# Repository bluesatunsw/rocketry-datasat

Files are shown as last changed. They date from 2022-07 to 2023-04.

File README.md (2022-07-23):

# rocketry-datasat
Cubesat-shaped data collection payload for Rocketry's Griffon rocket. Intended as a simple payload for the launch with the added benefit of being a helpful exercise for our satellite team. Deployment and recovery are not our problem.

## Specifications
- L3 M1590 motor.
- 1U cubesat formfactor (100mm\*100mm\*100mm).
- Practically unlimited weight limit.
- < 45 minutes waiting time on pad; system batteries must last this long at least.
- Max idle temperature on pad: 50 degrees.
- 4.74 seconds acceleration, at least that long decceleration, but probably longer. Up to 50G.
- Apogee (altitude ceiling): 3050 metres.

## Git Hygiene guide

For this project we will be using standard software engineering principles for our version control.

### Branches and forks

The most important of these is to **make sure to make a fresh pull request for every new feature**. If you want to work on the main repo, this also means a new branch for every feature. If you are using forks, you can branch as you please.

In this case a "feature" is any atomic piece of work you might be contributing, i.e. small enough that you are the only one likely to be working on it. For example, if you are working in /hardware you might implement the module to translate celestial coordinates to motor positions as a feature.

In the case that you are working on a bigger part with another person (or people) you can make a branch with sub-branches for each feature.

### Code review and pull requests

**Never commit directly to main**. The only exception to this is for making administrative changes like editing the readme, .gitignore, .codeowners and so on.
Whenever you finish a feature on a branch like described above, you should submit a **pull request** to get it merged back into a parent branch. Pull requests are also known as "merge requests" on GitLab and some other services (far clearer name frankly) because they basically give you a chance to write up what you've done and documents all the changes you are going to make. It also lets you safely specify how you are going to handle any conflicts between your branch and the parent.

Once you have made your pull request you should ideally get somebody else who didn't contribute to do a **code review** for you. This is mostly important on larger features or things where a lot can go wrong. While this project doesn't have critical stakes or a deployment to risk, it's a very important habit and will often catch a lot of mistakes that are very hard to find on your own (especially when they are errors in design rather than in code).

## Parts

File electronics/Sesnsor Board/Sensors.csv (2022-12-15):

Source: | D:\Sensor Board\Sensors\Sensors.kicad_sch
Date: | 14/10/2022 6:08:25 PM
Tool: | Eeschema (6.0.6)
Generator: | C:\Program Files\KiCad\6.0\bin\scripting\plugins/bom_csv_grouped_by_value.py
Component Count: | 15
Individual Components:
Item | Qty | Reference(s) | Value | LibPart | Footprint | Datasheet | MANUFACTURER | MAXIMUM_PACKAGE_HEIGHT | PARTREV | STANDARD
 |  | Board1 | Rocket_Board | BlueSat:Rocket_Board | IMU:Rocket_Layout
 |  | C1 | 1 uF | Device:C | Capacitor_SMD:C_0201_0603Metric_Pad0.64x0.40mm_HandSolder | ~
 |  | J1 | GY-91 | Connector:Conn_01x08_Female | Connector_PinHeader_2.54mm:PinHeader_1x08_P2.54mm_Vertical | ~
 |  | J2 | JTAG | Connector_Generic:Conn_01x04 | Connector_PinHeader_2.54mm:PinHeader_1x04_P2.54mm_Vertical | ~
 |  | J3 | UART | Connector_Generic:Conn_01x04 | Connector_PinHeader_2.54mm:PinHeader_1x04_P2.54mm_Vertical | ~
 |  | MicroSD1 | Conn_01x06 | Connector_Generic:Conn_01x06 | Connector_PinHeader_2.54mm:PinHeader_1x06_P2.54mm_Vertical | ~
 |  | PC1 | C | Device:C | Capacitor_SMD:C_0201_0603Metric_Pad0.64x0.40mm_HandSolder | ~
 |  | R1 | 10K | Device:R | Resistor_SMD:R_0201_0603Metric_Pad0.64x0.40mm_HandSolder | ~
 |  | R_{SCL}1 | 4,7K | Device:R_Small | Resistor_SMD:R_0603_1608Metric_Pad0.98x0.95mm_HandSolder | ~
 |  | R_{SDA}1 | 4,7K | Device:R_Small | Resistor_SMD:R_0603_1608Metric_Pad0.98x0.95mm_HandSolder | ~
 |  | Si7021 | Conn_01x05 | Connector_Generic:Conn_01x05 | Connector_PinHeader_2.54mm:PinHeader_1x05_P2.54mm_Vertical | ~
 |  | SW1 | SW_Push | Switch:SW_Push | Button_Switch_SMD:SW_SPST_B3U-1000P | ~
 |  | SW2 | SW_Push | Switch:SW_Push | Button_Switch_SMD:SW_SPST_B3U-1000P | ~
 |  | U1 | ESP32-WROOM-E | ESP32:ESP32-WROOM-E | Espressif:ESP32-WROOM-32E | https://www.espressif.com/sites/default/files/documentation/esp32-wroom-32e_esp32-wroom-32ue_datasheet_en.pdf
 |  | U2 | H3LIS100DLTR | IMU:H3LIS100DLTR | PQFN50P300X300X100-16N |  | STMicroelectronics | 1 mm | 2 | IPC 7351B
Collated Components:
Item | Qty | Reference(s) | Value | LibPart | Footprint | Datasheet | MANUFACTURER | MAXIMUM_PACKAGE_HEIGHT | PARTREV | STANDARD
1 | 1 | Board1 | Rocket_Board | BlueSat:Rocket_Board | IMU:Rocket_Layout
2 | 1 | C1 | 1 uF | Device:C | Capacitor_SMD:C_0201_0603Metric_Pad0.64x0.40mm_HandSolder | ~
3 | 1 | J1 | GY-91 | Connector:Conn_01x08_Female | Connector_PinHeader_2.54mm:PinHeader_1x08_P2.54mm_Vertical | ~
4 | 1 | J2 | JTAG | Connector_Generic:Conn_01x04 | Connector_PinHeader_2.54mm:PinHeader_1x04_P2.54mm_Vertical | ~
5 | 1 | J3 | UART | Connector_Generic:Conn_01x04 | Connector_PinHeader_2.54mm:PinHeader_1x04_P2.54mm_Vertical | ~
6 | 1 | MicroSD1 | Conn_01x06 | Connector_Generic:Conn_01x06 | Connector_PinHeader_2.54mm:PinHeader_1x06_P2.54mm_Vertical | ~
7 | 1 | PC1 | C | Device:C | Capacitor_SMD:C_0201_0603Metric_Pad0.64x0.40mm_HandSolder | ~
8 | 1 | R1 | 10K | Device:R | Resistor_SMD:R_0201_0603Metric_Pad0.64x0.40mm_HandSolder | ~
9 | 2 | R_{SCL}1, R_{SDA}1 | 4,7K | Device:R_Small | Resistor_SMD:R_0603_1608Metric_Pad0.98x0.95mm_HandSolder | ~
10 | 1 | Si7021 | Conn_01x05 | Connector_Generic:Conn_01x05 | Connector_PinHeader_2.54mm:PinHeader_1x05_P2.54mm_Vertical | ~
11 | 2 | SW1, SW2 | SW_Push | Switch:SW_Push | Button_Switch_SMD:SW_SPST_B3U-1000P | ~
12 | 1 | U1 | ESP32-WROOM-E | ESP32:ESP32-WROOM-E | Espressif:ESP32-WROOM-32E | https://www.espressif.com/sites/default/files/documentation/esp32-wroom-32e_esp32-wroom-32ue_datasheet_en.pdf
13 | 1 | U2 | H3LIS100DLTR | IMU:H3LIS100DLTR | PQFN50P300X300X100-16N |  | STMicroelectronics | 1 mm | 2 | IPC 7351B

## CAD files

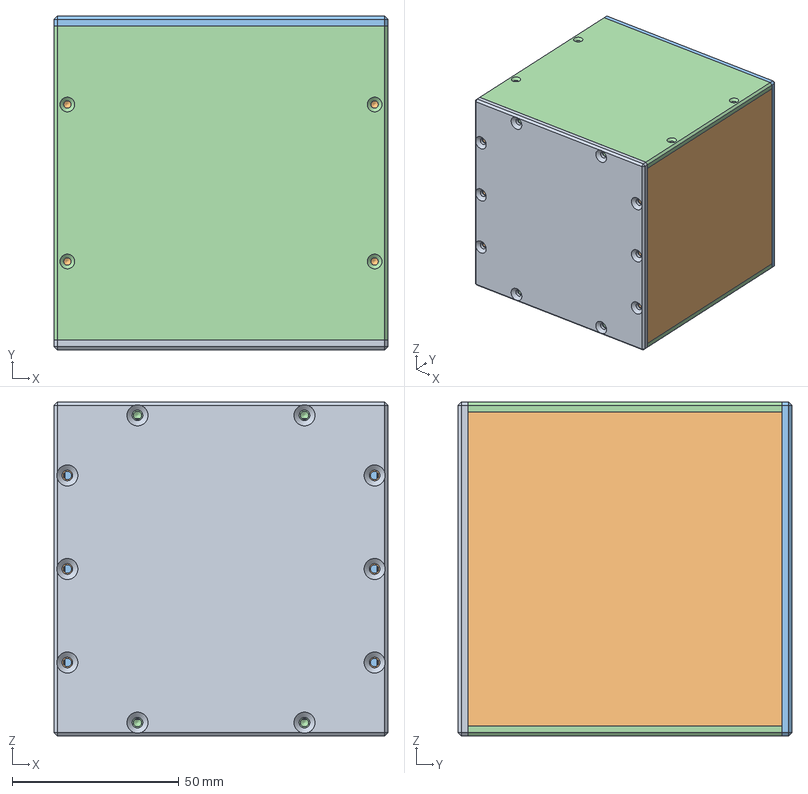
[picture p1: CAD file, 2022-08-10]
Structure/V2/1U_Satellite.stp
100.0 x 100.0 x 100.0 mm
TopPanel
LeftPanel
TopPanel_1
FrontPanel
LeftPanel_1
FrontPanel_1

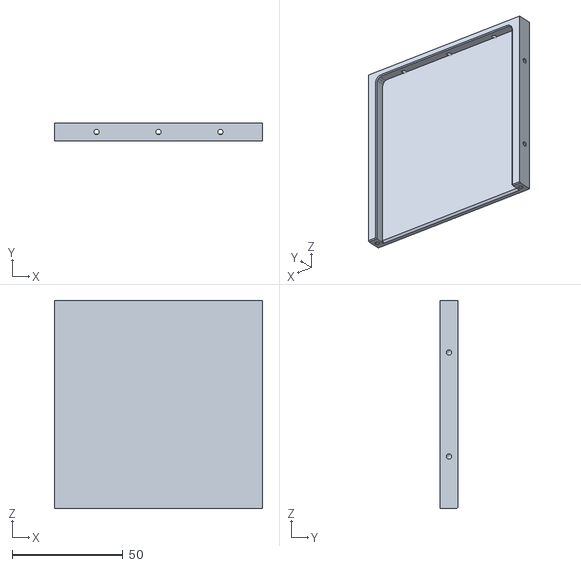
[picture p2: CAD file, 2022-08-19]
Structure/V2/STLs/LeftPanel.stl
94.0 x 8.00 x 94.0

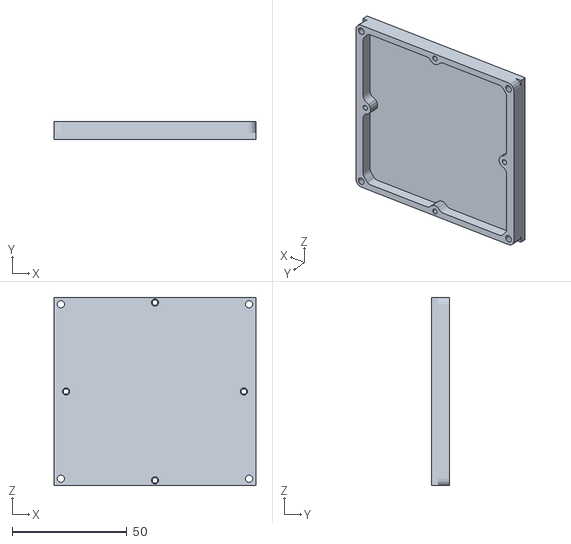
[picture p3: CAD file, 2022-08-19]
Structure/V2/STLs/ElectronicsBay.stl
88.0 x 8.00 x 82.0

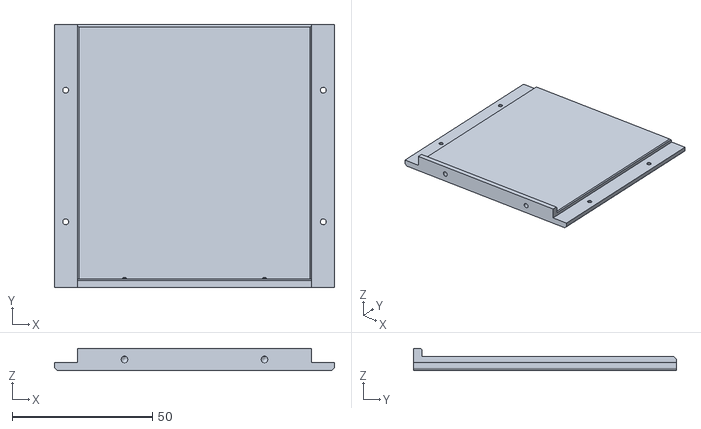
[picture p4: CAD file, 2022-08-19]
Structure/V2/STLs/FrontPanel.stl
100.0 x 94.0 x 8.00

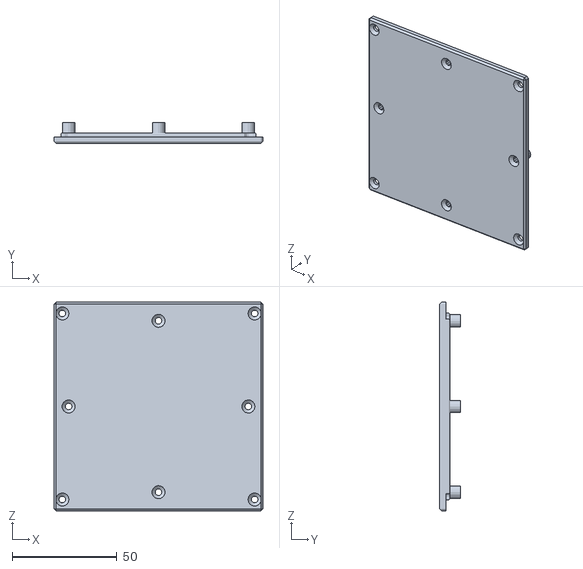
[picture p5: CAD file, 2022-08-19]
Structure/V2/STLs/TopPanel.stl
100.0 x 10.0 x 100.0

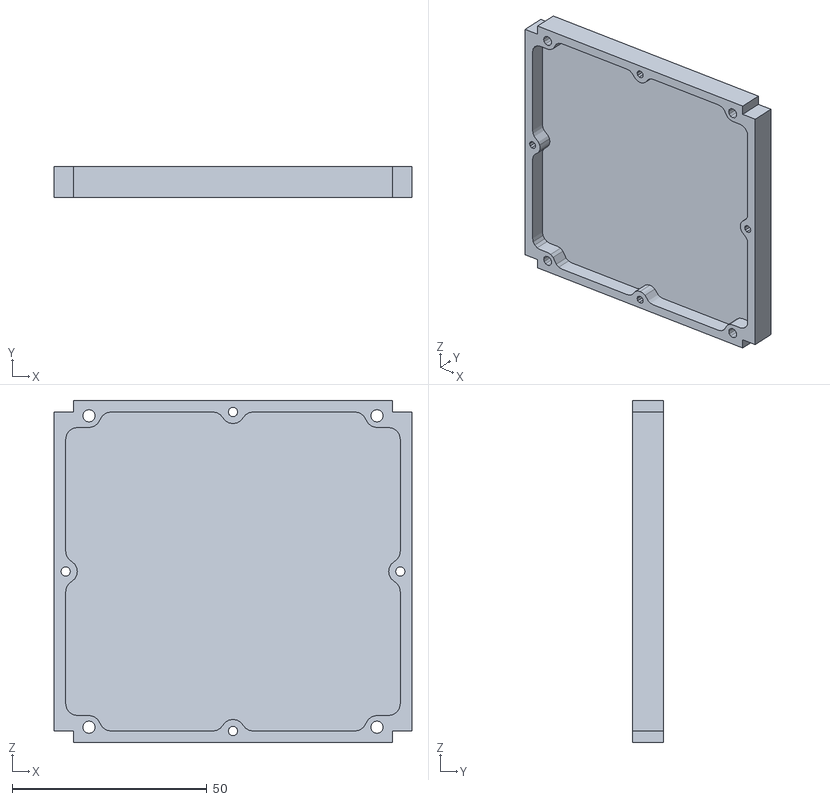
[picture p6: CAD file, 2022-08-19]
Structure/V2/STLs/ElectronicsBayUpper.stl
92.0 x 8.00 x 88.0

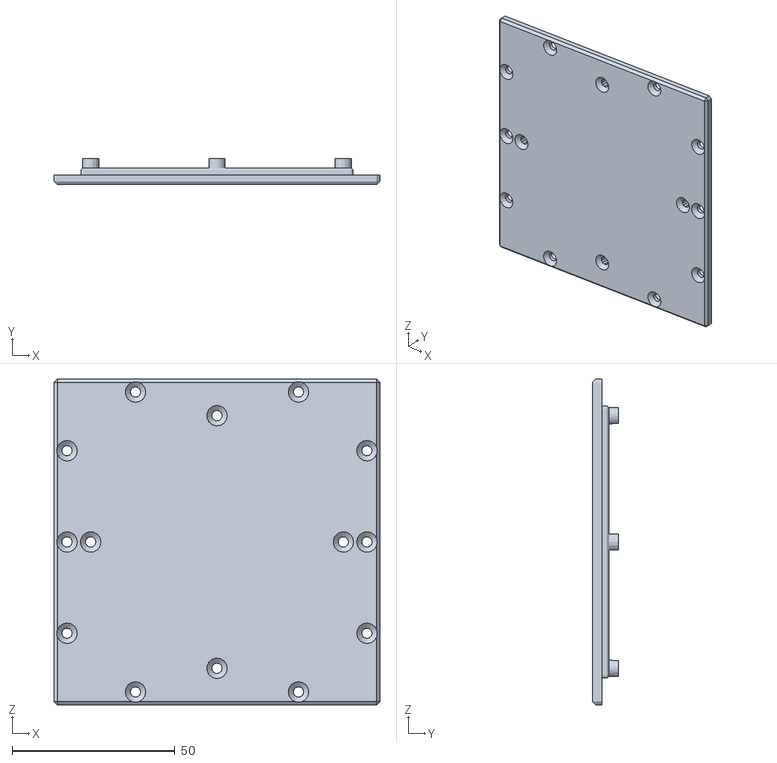
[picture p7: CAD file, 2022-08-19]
Structure/V2/STLs/BottomPanel.stl
100.0 x 8.00 x 100.0

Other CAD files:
Structure/V2/STLs/RightPanel.stl
Structure/V2/STLs/BackPanel.stl
Structure/Electronics_Structure/Battery_V1/BatteryHolderBottom.ipt
Structure/Electronics_Structure/Battery_V1/BatteryHolderEnd.ipt
Structure/Electronics_Structure/Battery_V1/BatteryHolderEndSeries.ipt
Structure/Electronics_Structure/Battery_V1/BatteryHolderTop.ipt
Structure/Electronics_Structure/Battery_V1/BatteryPack.iam
Structure/Electronics_Structure/Battery_V1/BatteryStandoff.ipt
Structure/Electronics_Structure/Battery_V1/OldVersions/BatteryHolder.0001.ipt
Structure/Electronics_Structure/Battery_V1/OldVersions/BatteryHolderBottom.0004.ipt
Structure/Electronics_Structure/Battery_V1/OldVersions/BatteryHolderEnd.0005.ipt
Structure/Electronics_Structure/Battery_V1/OldVersions/BatteryHolderEnd.0006.ipt
Structure/Electronics_Structure/Battery_V1/OldVersions/BatteryHolderEndSeries.0008.ipt
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

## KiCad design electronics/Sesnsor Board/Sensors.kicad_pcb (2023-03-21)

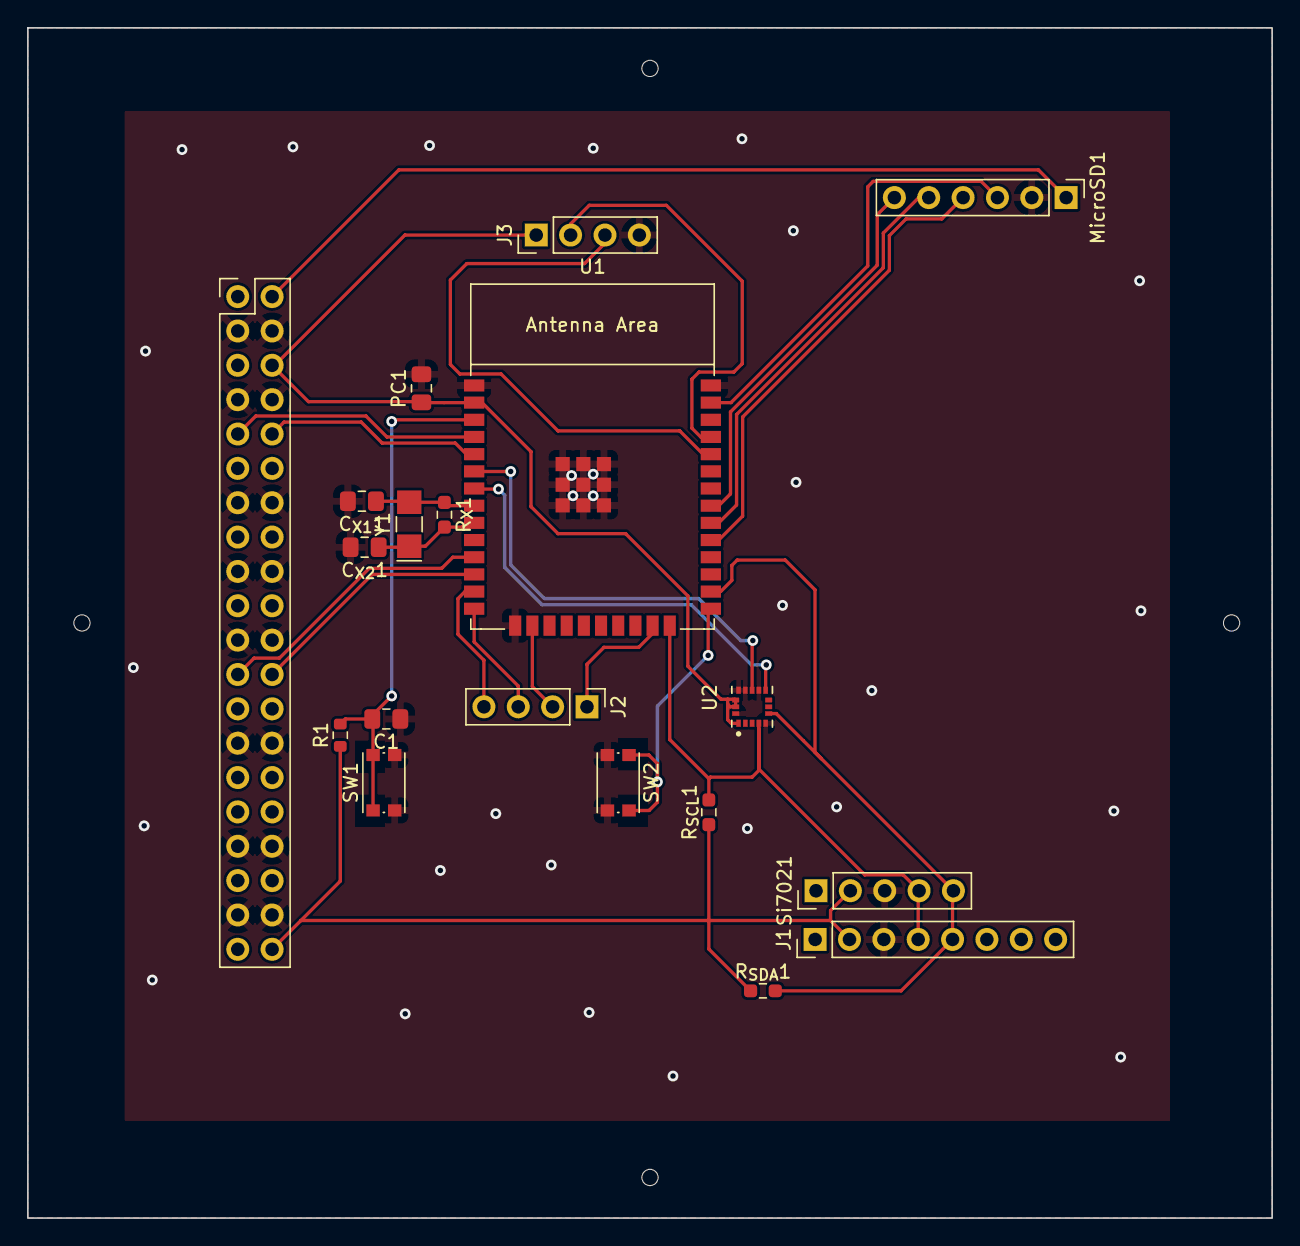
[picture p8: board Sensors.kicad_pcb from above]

Board: 2 copper layers, 92.0 x 88.0 mm, 19 parts (0 on the bottom side), 25 nets.

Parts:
Board1: Rocket_Board; Rocket_Layout
C1: 1uF; C_0805_2012Metric_Pad1.18x1.45mm_HandSolder
C_{X1}1, C_{X2}1: 25pF; C_0805_2012Metric_Pad1.18x1.45mm_HandSolder
J1: GY-91; PinHeader_1x08_P2.54mm_Vertical
J2: JTAG; PinHeader_1x04_P2.54mm_Vertical
J3: UART; PinHeader_1x04_P2.54mm_Vertical
MicroSD1: Conn_01x06; PinHeader_1x06_P2.54mm_Vertical
PC1: 22uF; C_0805_2012Metric_Pad1.18x1.45mm_HandSolder
R1: 10K; R_0603_1608Metric
R_{SCL}1: 4,7K; R_0603_1608Metric_Pad0.98x0.95mm_HandSolder
R_{SDA}1: 4,7K; R_0603_1608Metric_Pad0.98x0.95mm_HandSolder
R_{X}1: 7.5M; R_0603_1608Metric_Pad0.98x0.95mm_HandSolder
SW1, SW2: SW_Push; SW_Push_1P1T_NO_CK_KMR2
Si7021: Conn_01x05; PinHeader_1x05_P2.54mm_Vertical
U1: ESP32-WROOM-E; ESP32-WROOM-32E
U2: H3LIS100DLTR; PQFN50P300X300X100-16N
Y1: 32.768; Crystal_SMD_G8-2Pin_3.2x1.5mm_HandSoldering

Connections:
+3V3: Board1.3 (3.3V), Board1.10 (3.3V), Board1.20 (3.3V), Board1.21 (3.3V), Board1.31 (3.3V), Board1.38 (3.3V), J1.2, J3.1, PC1.1, R1.1, R_{SCL}1.1, R_{SDA}1.1, Si7021.2, U1.2 (3V3), U2.1 (VDD_IO), U2.14 (VDD), U2.15 (VDD)
+5V: Board1.1 (5V), Board1.8 (5V), Board1.18 (5V), Board1.23 (5V), Board1.33 (5V), Board1.40 (5V), MicroSD1.1
/I34: U1.6 (GPIO34/ADC1_CH6), U2.11 (INT1)
/I35: U1.7 (GPIO35/ADC1_CH7), U2.9 (INT2)
/I36: Board1.5 (D1), U1.4 (SENSOR_VP/GPIO36/ADC1_CH0)
/I39: Board1.36 (D2), U1.5 (SENSOR_VN/GPIO39/ADC1_CH3)
/IO0: SW2.1, U1.25 (GPIO0/BOOT/ADC2_CH1)
/IO1: J3.2, U1.35 (U0TXD/GPIO1)
/IO2: J1.4, R_{SCL}1.2, Si7021.4, U1.24 (ADC2_CH2/GPIO2), U2.4 (SCL/SPC)
/IO3: J3.3, U1.34 (U0RXD/GPIO3)
/IO4: J1.5, R_{SDA}1.2, Si7021.5, U1.26 (ADC2_CH0/GPIO4), U2.6 (SDA/SDI/SDO)
/IO5: MicroSD1.4, U1.29 (GPIO5)
/IO12: J2.3, U1.14 (MTDI/GPIO12/ADC2_CH5)
/IO13: J2.2, U1.16 (MTCK/GPIO13/ADC2_CH4)
/IO14: J2.4, U1.13 (MTMS/GPIO14/ADC2_CH6)
/IO15: J2.1, U1.23 (MTDO/GPIO15/ADC2_CH3)
/IO18: MicroSD1.5, U1.30 (GPIO18)
/IO19: MicroSD1.6, U1.31 (GPIO19)
/IO23: MicroSD1.3, U1.37 (GPIO23)
/IO26: Board1.12 (D5), U1.11 (DAC_2/ADC2_CH9/GPIO26)
/IO27: Board1.29 (D6), U1.12 (ADC2_CH7/GPIO27)
/IO32: C_{X1}1.1, R_{X}1.1, U1.8 (32K_XP/GPIO32/ADC1_CH4), Y1.2
/IO33: C_{X2}1.1, R_{X}1.2, U1.9 (32K_XN/GPIO33/ADC1_CH5), Y1.1
GND: Board1.2 (GND), Board1.4 (GND), Board1.7 (GND), Board1.9 (GND), Board1.11 (GND), Board1.14 (GND), Board1.17 (GND), Board1.19 (GND), Board1.22 (GND), Board1.24 (GND), Board1.27 (GND), Board1.30 (GND), Board1.32 (GND), Board1.34 (GND), Board1.37 (GND), Board1.39 (GND), C1.1, C_{X1}1.2, C_{X2}1.2, J1.3, J3.4, MicroSD1.2, PC1.2, SW1.2, SW2.2, Si7021.3, U1.1 (GND), U1.15 (GND), U1.38 (GND), U1.39 (GND_THERMAL), U2.5 (GND), U2.10 (GND), U2.12 (GND), U2.13 (GND), U2.16 (GND)
unnamed: C1.2, R1.2, SW1.1, U1.3 (EN/CHIP_PU)

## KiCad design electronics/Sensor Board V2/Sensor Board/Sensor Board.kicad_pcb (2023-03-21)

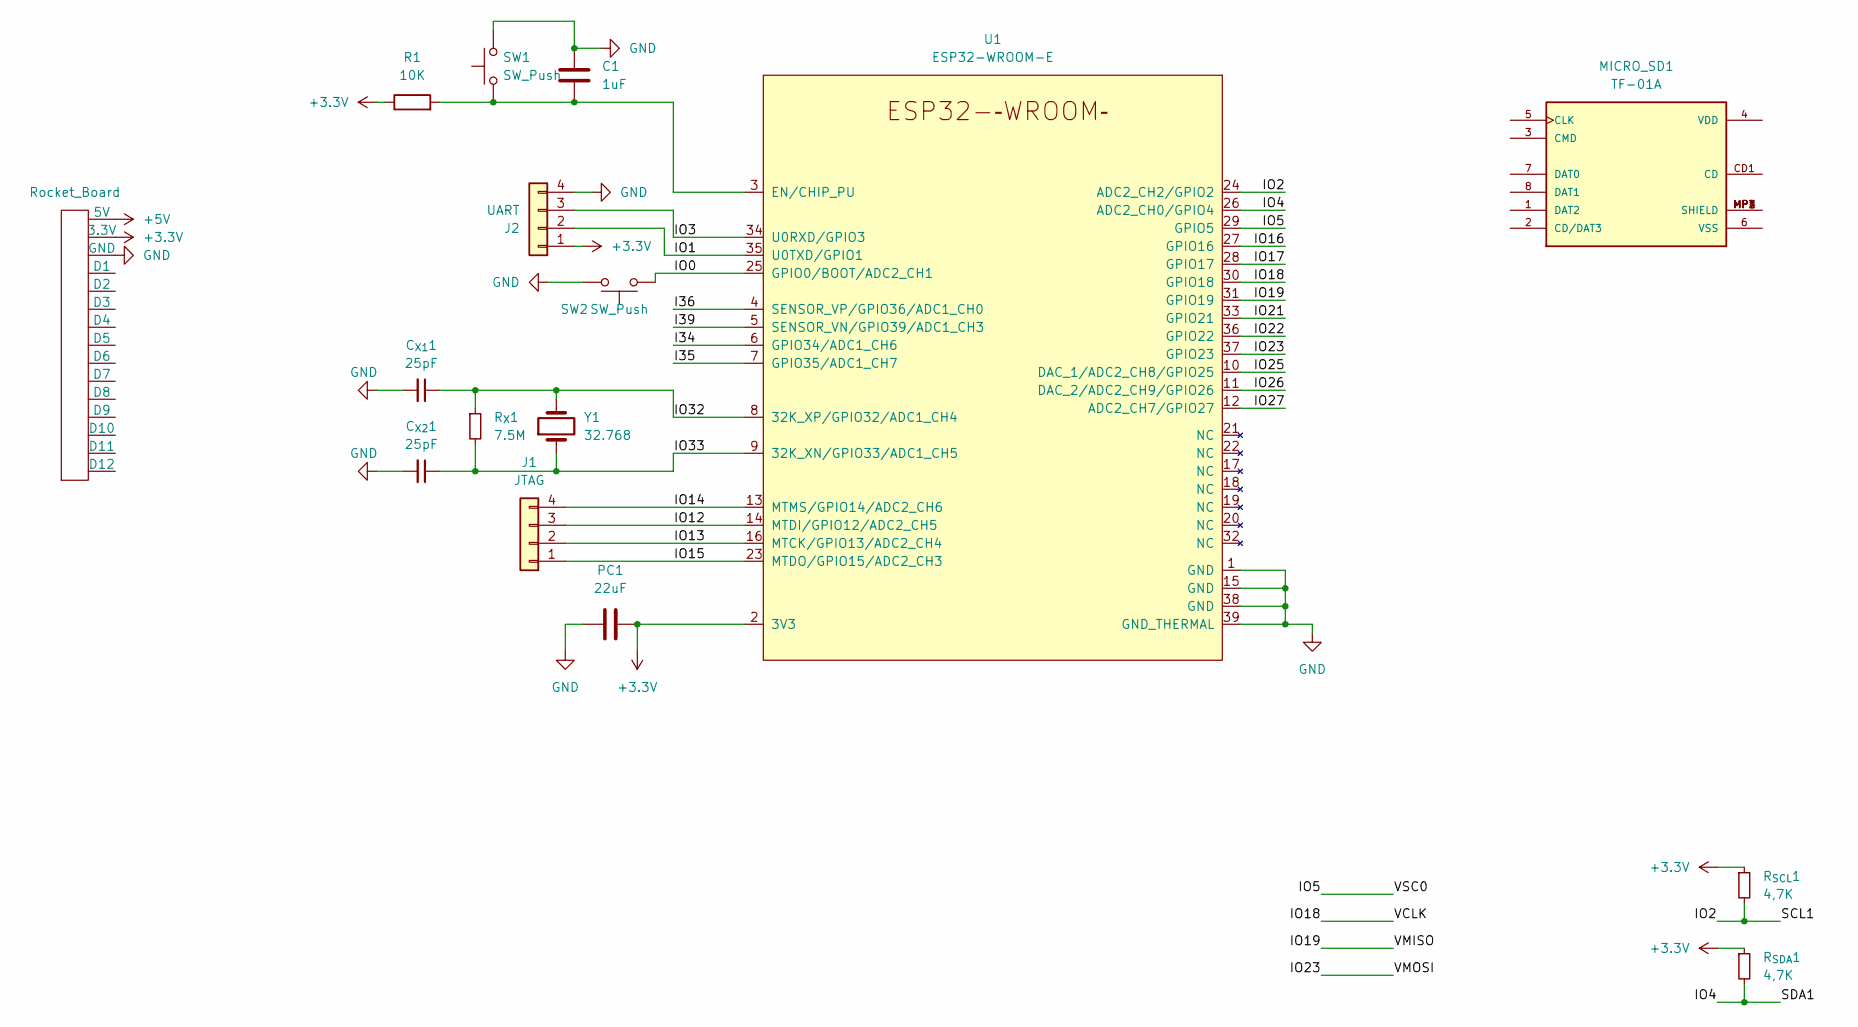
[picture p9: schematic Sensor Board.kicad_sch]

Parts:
Board1: Rocket_Board; Rocket_Layout
C1: 1uF; C_0805_2012Metric_Pad1.18x1.45mm_HandSolder
C_{X1}1, C_{X2}1: 25pF; C_0805_2012Metric_Pad1.18x1.45mm_HandSolder
J1: JTAG; PinHeader_1x04_P2.54mm_Vertical
J2: UART; PinHeader_1x04_P2.54mm_Vertical
MICRO_SD1: TF-01A
PC1: 22uF; C_0805_2012Metric_Pad1.18x1.45mm_HandSolder
R1: 10K; R_0603_1608Metric
R_{SCL}1: 4,7K; R_0603_1608Metric_Pad0.98x0.95mm_HandSolder
R_{SDA}1: 4,7K; R_0603_1608Metric_Pad0.98x0.95mm_HandSolder
R_{X}1: 7.5M; R_0603_1608Metric_Pad0.98x0.95mm_HandSolder
SW1, SW2: SW_Push; SW_Push_1P1T_NO_CK_KMR2
U1: ESP32-WROOM-E; ESP32-WROOM-32E
Y1: 32.768; Crystal_SMD_G8-2Pin_3.2x1.5mm_HandSoldering

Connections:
+3V3: Board1.3 (3.3V), Board1.10 (3.3V), Board1.20 (3.3V), Board1.21 (3.3V), Board1.31 (3.3V), Board1.38 (3.3V), J2.1, PC1.1, R1.1, R_{SCL}1.1, R_{SDA}1.1, U1.2 (3V3)
+5V: Board1.1 (5V), Board1.8 (5V), Board1.18 (5V), Board1.23 (5V), Board1.33 (5V), Board1.40 (5V)
/I34: U1.6 (GPIO34/ADC1_CH6)
/I35: U1.7 (GPIO35/ADC1_CH7)
/I36: U1.4 (SENSOR_VP/GPIO36/ADC1_CH0)
/I39: U1.5 (SENSOR_VN/GPIO39/ADC1_CH3)
/IO0: SW2.1, U1.25 (GPIO0/BOOT/ADC2_CH1)
/IO1: J2.2, U1.35 (U0TXD/GPIO1)
/IO2: R_{SCL}1.2, U1.24 (ADC2_CH2/GPIO2)
/IO3: J2.3, U1.34 (U0RXD/GPIO3)
/IO4: R_{SDA}1.2, U1.26 (ADC2_CH0/GPIO4)
/IO5: U1.29 (GPIO5)
/IO12: J1.3, U1.14 (MTDI/GPIO12/ADC2_CH5)
/IO13: J1.2, U1.16 (MTCK/GPIO13/ADC2_CH4)
/IO14: J1.4, U1.13 (MTMS/GPIO14/ADC2_CH6)
/IO15: J1.1, U1.23 (MTDO/GPIO15/ADC2_CH3)
/IO16: U1.27 (GPIO16)
/IO17: U1.28 (GPIO17)
/IO18: U1.30 (GPIO18)
/IO19: U1.31 (GPIO19)
/IO21: U1.33 (GPIO21)
/IO22: U1.36 (GPIO22)
/IO23: U1.37 (GPIO23)
/IO25: U1.10 (DAC_1/ADC2_CH8/GPIO25)
/IO26: U1.11 (DAC_2/ADC2_CH9/GPIO26)
/IO27: U1.12 (ADC2_CH7/GPIO27)
/IO32: C_{X1}1.1, R_{X}1.1, U1.8 (32K_XP/GPIO32/ADC1_CH4), Y1.2
/IO33: C_{X2}1.1, R_{X}1.2, U1.9 (32K_XN/GPIO33/ADC1_CH5), Y1.1
GND: Board1.2 (GND), Board1.4 (GND), Board1.7 (GND), Board1.9 (GND), Board1.11 (GND), Board1.14 (GND), Board1.17 (GND), Board1.19 (GND), Board1.22 (GND), Board1.24 (GND), Board1.27 (GND), Board1.30 (GND), Board1.32 (GND), Board1.34 (GND), Board1.37 (GND), Board1.39 (GND), C1.1, C_{X1}1.2, C_{X2}1.2, J2.4, PC1.2, SW1.2, SW2.2, U1.1 (GND), U1.15 (GND), U1.38 (GND), U1.39 (GND_THERMAL)
unnamed: C1.2, R1.2, SW1.1, U1.3 (EN/CHIP_PU)
unnamed: MICRO_SD1.MP1 (SHIELD), MICRO_SD1.MP2 (SHIELD), MICRO_SD1.MP3 (SHIELD), MICRO_SD1.MP4 (SHIELD)

Board: 2 copper layers, 16 parts (0 on the bottom side), 16 nets, no tracks yet.

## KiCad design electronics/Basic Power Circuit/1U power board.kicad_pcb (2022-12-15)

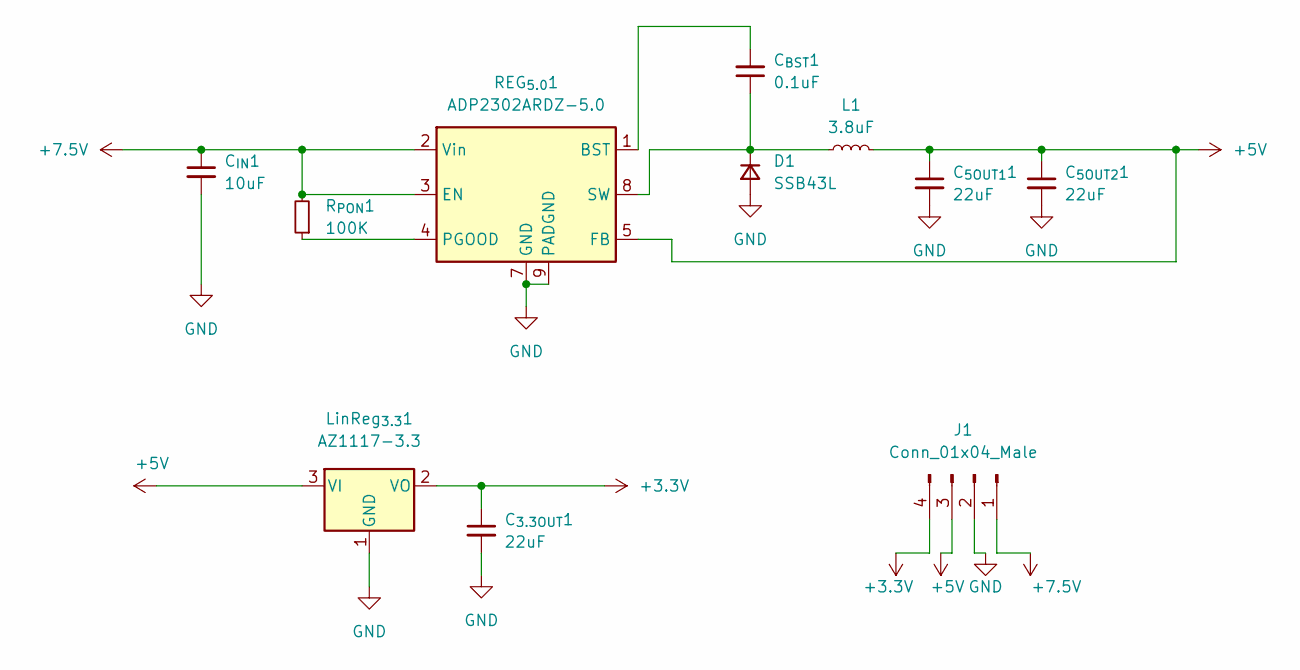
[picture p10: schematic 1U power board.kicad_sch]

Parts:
C_{3.3OUT}1, C_{5OUT1}1, C_{5OUT2}1: 22uF; C_0603_1608Metric_Pad1.08x0.95mm_HandSolder
C_{BST}1: 0.1uF; C_0603_1608Metric_Pad1.08x0.95mm_HandSolder
C_{IN}1: 10uF; C_0603_1608Metric_Pad1.08x0.95mm_HandSolder
D1: SSB43L; SSB43L hand solder
J1: Conn_01x04_Male; PinHeader_1x04_P2.54mm_Vertical
L1: 3.8uF; CDRH104R inductor
LinReg_{3.3}1: AZ1117-3.3; TO-252-2
REG_{5.0}1: ADP2302ARDZ-5.0; SOIC-8-1EP_3.9x4.9mm_P1.27mm_EP2.29x3mm
R_{PON}1: 100K; R_0603_1608Metric_Pad0.98x0.95mm_HandSolder

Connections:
+3V3: C_{3.3OUT}1.1, J1.4, LinReg_{3.3}1.2 (VO)
+5V: C_{5OUT1}1.1, C_{5OUT2}1.1, J1.3, L1.2, LinReg_{3.3}1.3 (VI), REG_{5.0}1.5 (FB)
+7.5V: C_{IN}1.1, J1.1, REG_{5.0}1.2 (Vin), REG_{5.0}1.3 (EN), R_{PON}1.2
GND: C_{3.3OUT}1.2, C_{5OUT1}1.2, C_{5OUT2}1.2, C_{IN}1.2, D1.2 (A), J1.2, LinReg_{3.3}1.1 (GND), REG_{5.0}1.7 (GND), REG_{5.0}1.9 (PADGND)
unnamed: C_{BST}1.1, D1.1 (K), L1.1, REG_{5.0}1.8 (SW)
unnamed: C_{BST}1.2, REG_{5.0}1.1 (BST)
unnamed: REG_{5.0}1.4 (PGOOD), R_{PON}1.1

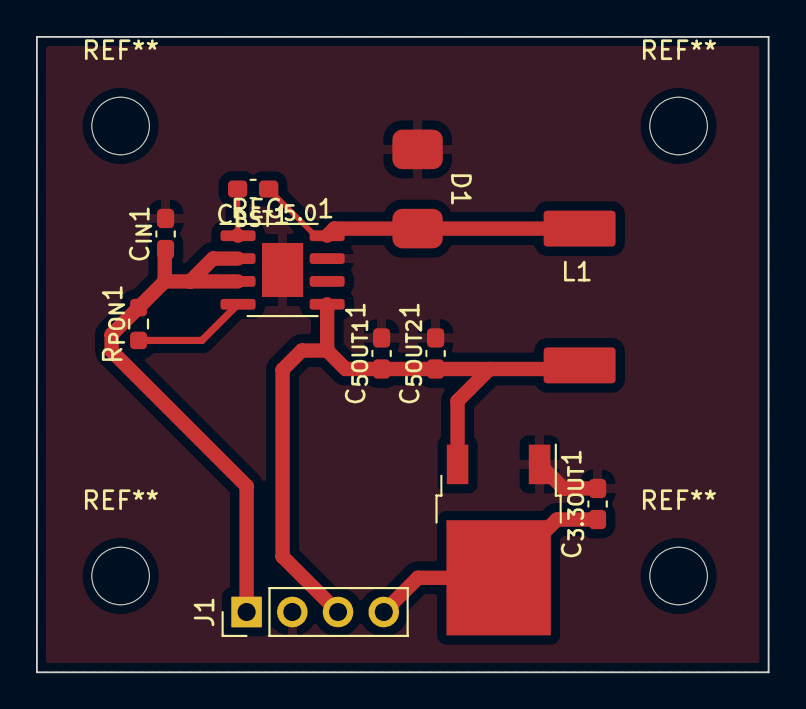
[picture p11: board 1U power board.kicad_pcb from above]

Board: 2 copper layers, 40.7 x 35.3 mm, 11 parts (0 on the bottom side), 7 nets.

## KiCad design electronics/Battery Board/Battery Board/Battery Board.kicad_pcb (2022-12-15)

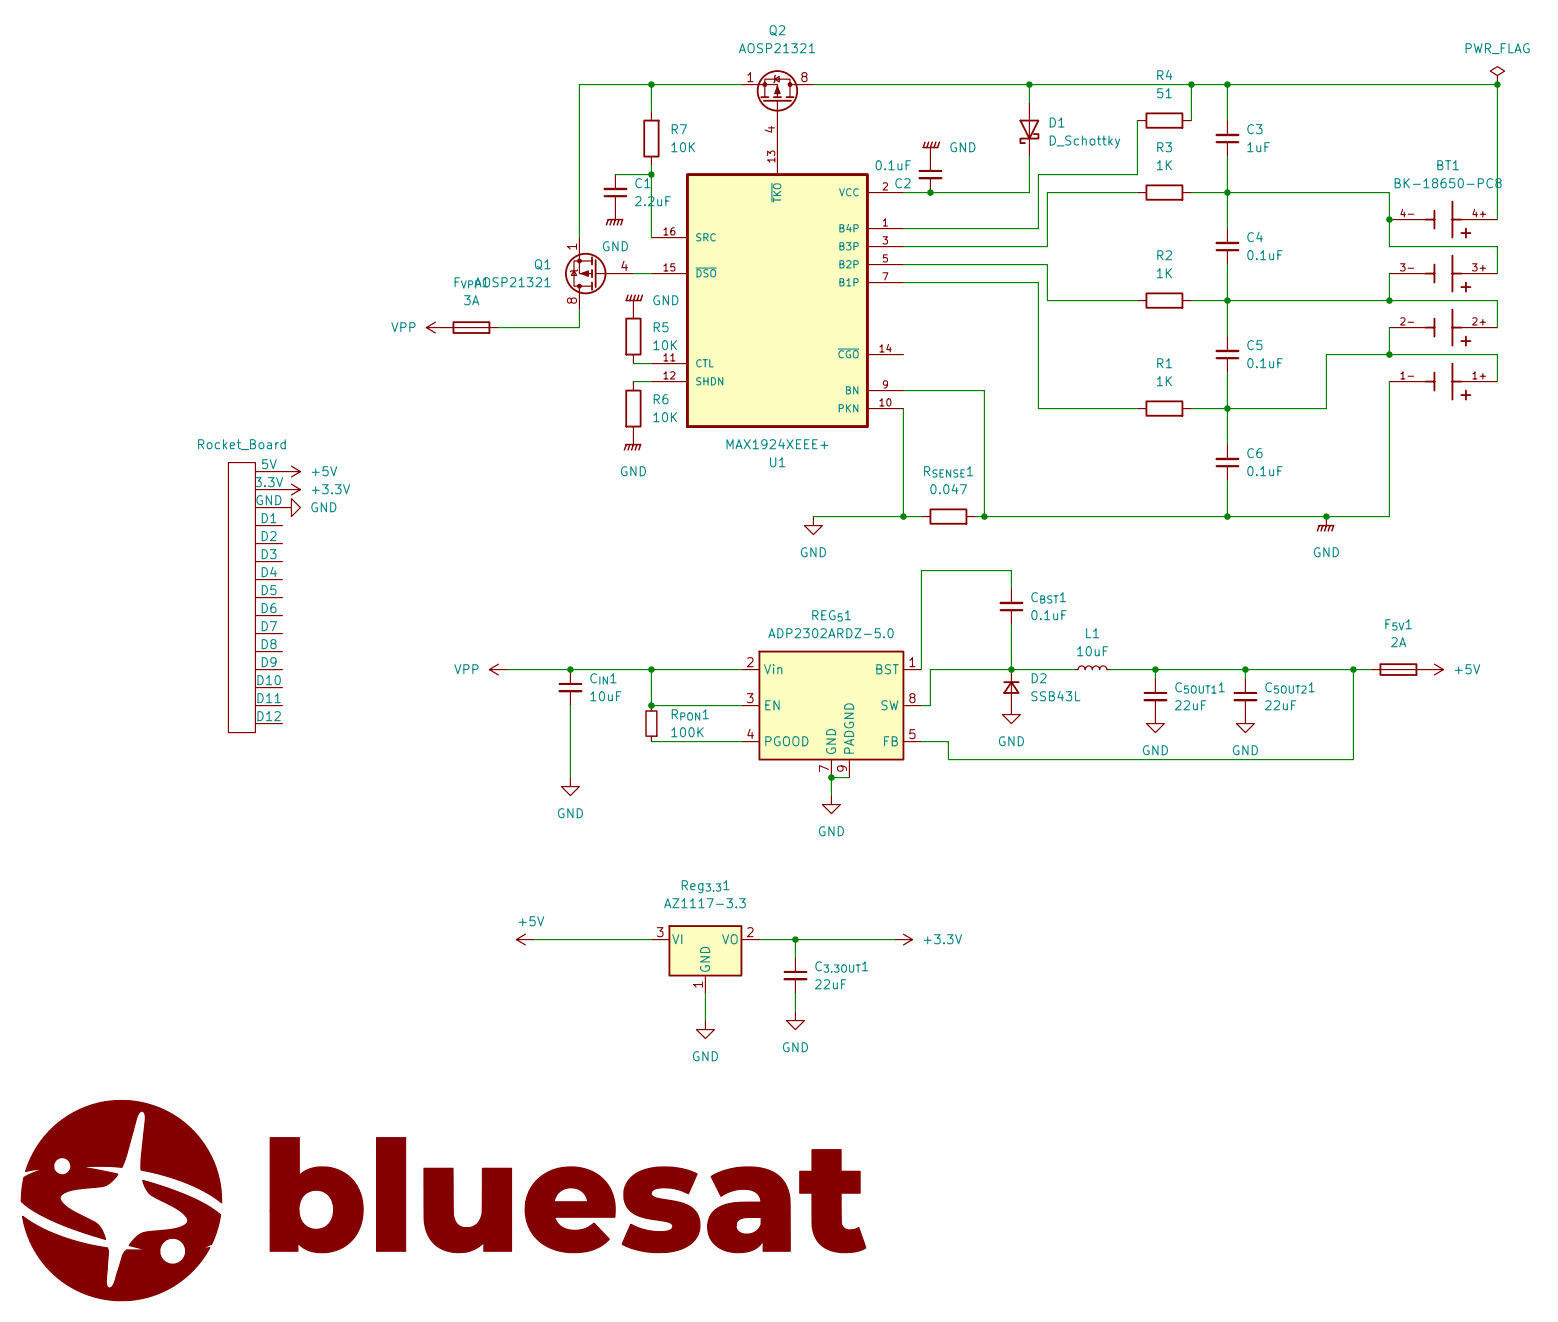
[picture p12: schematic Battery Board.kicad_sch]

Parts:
BT1: BK-18650-PC8; BAT_BK-18650-PC8; PARTREV L
C1: 2.2uF; C_0805_2012Metric_Pad1.18x1.45mm_HandSolder
C2, C4, C5, C6: 0.1uF; C_0805_2012Metric_Pad1.18x1.45mm_HandSolder
C3: 1uF; C_0805_2012Metric_Pad1.18x1.45mm_HandSolder
C_{3.3OUT}1, C_{5OUT1}1, C_{5OUT2}1: 22uF; C_0603_1608Metric_Pad1.08x0.95mm_HandSolder
C_{BST}1: 0.1uF; C_0603_1608Metric_Pad1.08x0.95mm_HandSolder
C_{IN}1: 10uF; C_0603_1608Metric_Pad1.08x0.95mm_HandSolder
D1: D_Schottky; SOT91P240X102-3N
D2: SSB43L; SSB43L hand solder
F_{5V}1: 2A; Fuse_1206_3216Metric_Pad1.42x1.75mm_HandSolder
F_{VPP}1: 3A; Fuse_1206_3216Metric_Pad1.42x1.75mm_HandSolder
L1: 10uF; CDRH104R inductor
Q1, Q2: AOSP21321; SOIC-8_3.9x4.9mm_P1.27mm
R1, R2, R3: 1K; R_0603_1608Metric_Pad0.98x0.95mm_HandSolder
R4: 51; R_0603_1608Metric_Pad0.98x0.95mm_HandSolder
R5, R6, R7: 10K; R_0603_1608Metric_Pad0.98x0.95mm_HandSolder
R8: Rocket_Board; Rocket_Layout
REG_{5}1: ADP2302ARDZ-5.0; SOIC-8-1EP_3.9x4.9mm_P1.27mm_EP2.29x3mm
R_{PON}1: 100K; R_0603_1608Metric_Pad0.98x0.95mm_HandSolder
R_{SENSE}1: 0.047; WSHP2818 Shunt resistor Vishay
Reg_{3.3}1: AZ1117-3.3; TO-252-2
U1: MAX1924XEEE+; SOP63P602X175-16N

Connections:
+3V3: C_{3.3OUT}1.1, R8.3 (3.3V), R8.10 (3.3V), R8.20 (3.3V), R8.21 (3.3V), R8.31 (3.3V), R8.38 (3.3V), Reg_{3.3}1.2 (VO)
+5V: F_{5V}1.2, R8.1 (5V), R8.8 (5V), R8.18 (5V), R8.23 (5V), R8.33 (5V), R8.40 (5V), Reg_{3.3}1.3 (VI)
unnamed: BT1.1+, BT1.2-, C5.1, C6.2, R1.2
unnamed: BT1.2+, BT1.3-, C4.1, C5.2, R2.2
unnamed: BT1.3+, BT1.4-, C3.1, C4.2, R3.2
unnamed: BT1.4+, C3.2, D1.2 (A), Q2.5 (D), Q2.6 (D), Q2.7 (D), Q2.8 (D), R4.2
unnamed: C1.2, R7.1, U1.16 (SRC)
unnamed: C_{5OUT1}1.1, C_{5OUT2}1.1, F_{5V}1.1, L1.2, REG_{5}1.5 (FB)
unnamed: C_{BST}1.1, D2.1 (K), L1.1, REG_{5}1.8 (SW)
unnamed: C_{BST}1.2, REG_{5}1.1 (BST)
unnamed: C2.2, D1.1 (K), U1.2 (VCC)
unnamed: Q1.1 (S), Q1.2 (S), Q1.3 (S), Q2.1 (S), Q2.2 (S), Q2.3 (S), R7.2
unnamed: Q1.4 (G), U1.15 (~DSO)
unnamed: F_{VPP}1.2, Q1.5 (D), Q1.6 (D), Q1.7 (D), Q1.8 (D)
unnamed: Q2.4 (G), U1.13 (~TKO)
unnamed: R1.1, U1.7 (B1P)
unnamed: R2.1, U1.5 (B2P)
unnamed: R3.1, U1.3 (B3P)
unnamed: R4.1, U1.1 (B4P)
unnamed: R5.2, U1.11 (CTL)
unnamed: R6.1, U1.12 (SHDN)
unnamed: REG_{5}1.4 (PGOOD), R_{PON}1.1
VPP: C_{IN}1.1, F_{VPP}1.1, REG_{5}1.2 (Vin), REG_{5}1.3 (EN), R_{PON}1.2

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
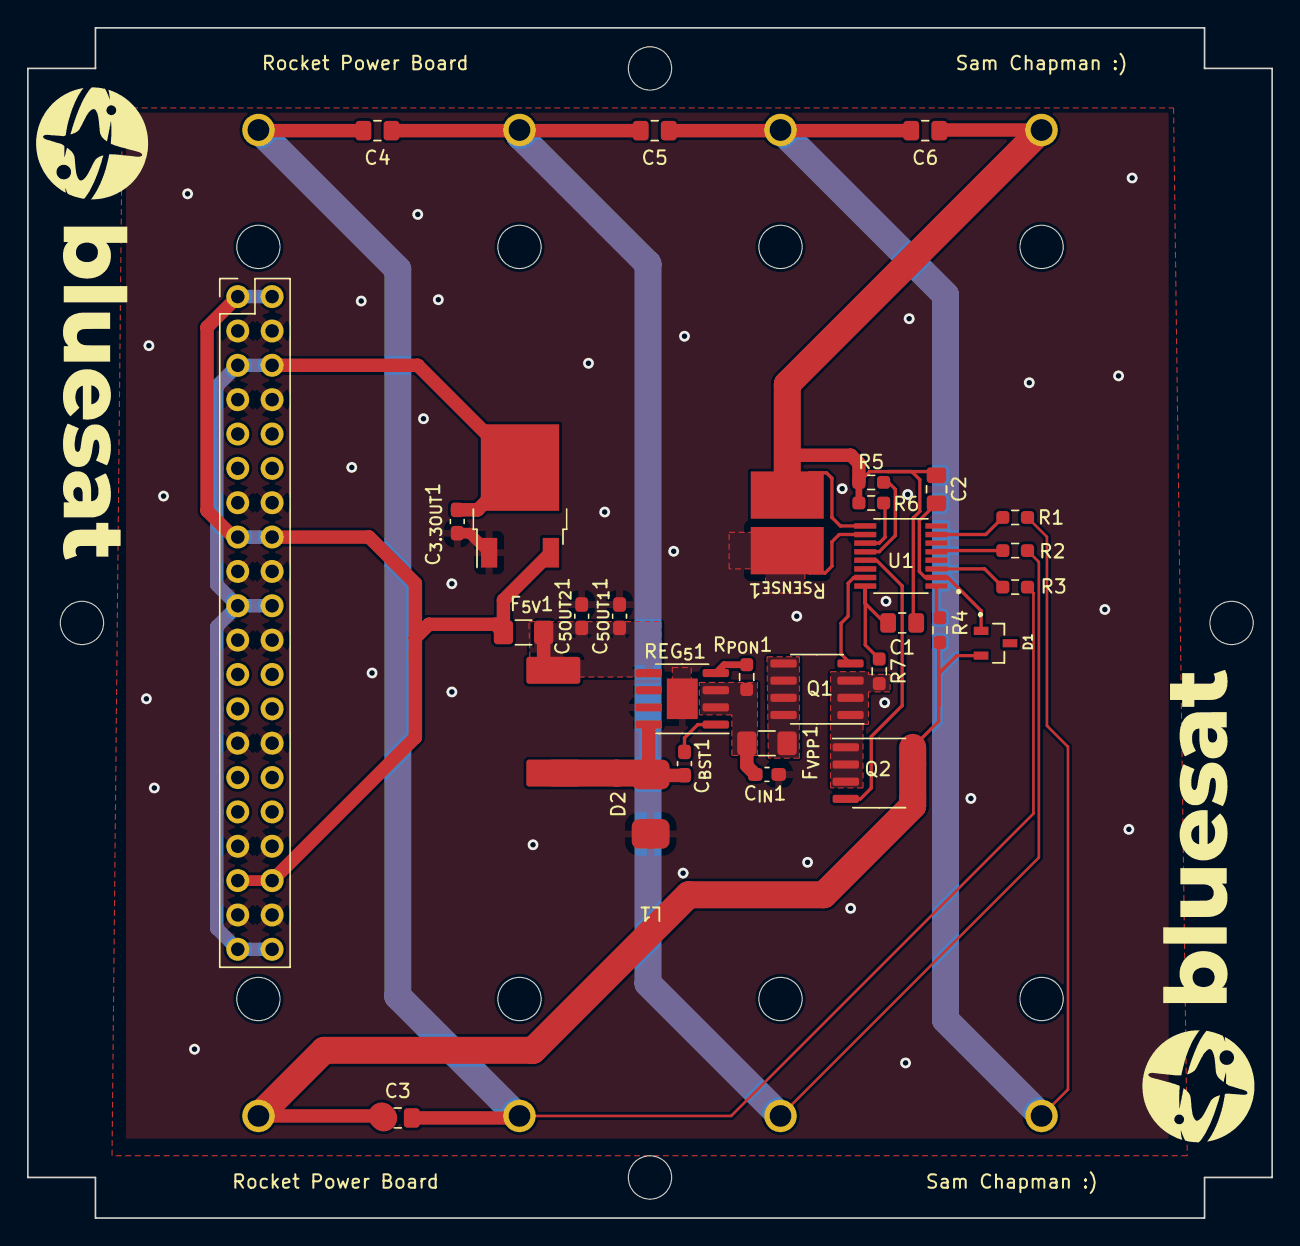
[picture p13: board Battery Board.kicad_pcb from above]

Board: 2 copper layers, 92.0 x 88.0 mm, 32 parts (1 on the bottom side), 25 nets.

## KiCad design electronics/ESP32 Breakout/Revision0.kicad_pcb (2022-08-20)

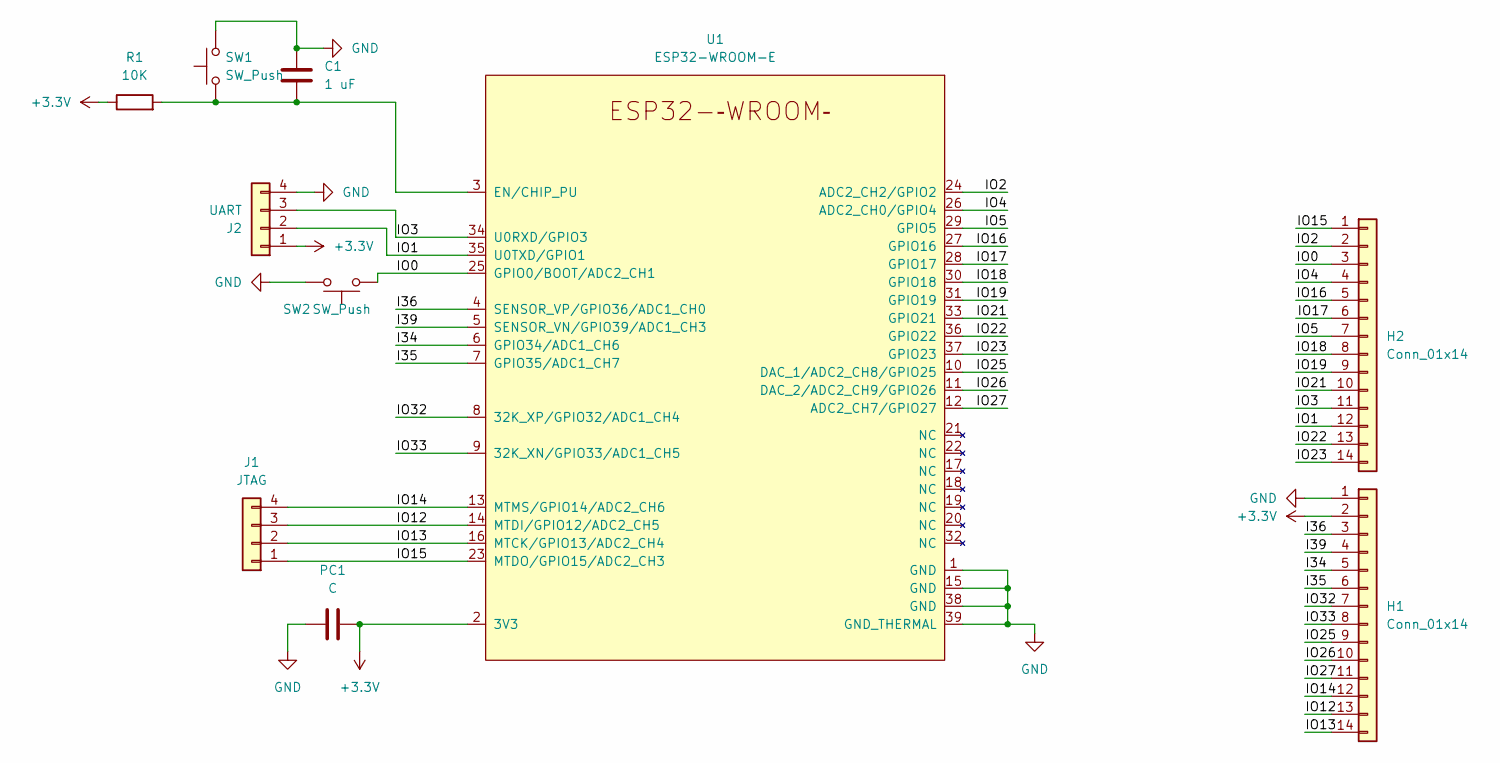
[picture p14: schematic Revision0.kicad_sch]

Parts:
C1: 1 uF; C_0201_0603Metric_Pad0.64x0.40mm_HandSolder
H1, H2: Conn_01x14; PinHeader_1x14_P2.54mm_Vertical
J1: JTAG; PinHeader_1x04_P2.54mm_Vertical
J2: UART; PinHeader_1x04_P2.54mm_Vertical
PC1: C; C_0201_0603Metric_Pad0.64x0.40mm_HandSolder
R1: 10K; R_0201_0603Metric_Pad0.64x0.40mm_HandSolder
SW1, SW2: SW_Push; SW_SPST_B3U-1000P
U1: ESP32-WROOM-E; ESP32-WROOM-32E

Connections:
+3V3: H1.2, J2.1, PC1.1, R1.1, U1.2 (3V3)
/I34: H1.5, U1.6 (GPIO34/ADC1_CH6)
/I35: H1.6, U1.7 (GPIO35/ADC1_CH7)
/I36: H1.3, U1.4 (SENSOR_VP/GPIO36/ADC1_CH0)
/I39: H1.4, U1.5 (SENSOR_VN/GPIO39/ADC1_CH3)
/IO0: H2.3, SW2.1, U1.25 (GPIO0/BOOT/ADC2_CH1)
/IO1: H2.12, J2.2, U1.35 (U0TXD/GPIO1)
/IO2: H2.2, U1.24 (ADC2_CH2/GPIO2)
/IO3: H2.11, J2.3, U1.34 (U0RXD/GPIO3)
/IO4: H2.4, U1.26 (ADC2_CH0/GPIO4)
/IO5: H2.7, U1.29 (GPIO5)
/IO12: H1.13, J1.3, U1.14 (MTDI/GPIO12/ADC2_CH5)
/IO13: H1.14, J1.2, U1.16 (MTCK/GPIO13/ADC2_CH4)
/IO14: H1.12, J1.4, U1.13 (MTMS/GPIO14/ADC2_CH6)
/IO15: H2.1, J1.1, U1.23 (MTDO/GPIO15/ADC2_CH3)
/IO16: H2.5, U1.27 (GPIO16)
/IO17: H2.6, U1.28 (GPIO17)
/IO18: H2.8, U1.30 (GPIO18)
/IO19: H2.9, U1.31 (GPIO19)
/IO21: H2.10, U1.33 (GPIO21)
/IO22: H2.13, U1.36 (GPIO22)
/IO23: H2.14, U1.37 (GPIO23)
/IO25: H1.9, U1.10 (DAC_1/ADC2_CH8/GPIO25)
/IO26: H1.10, U1.11 (DAC_2/ADC2_CH9/GPIO26)
/IO27: H1.11, U1.12 (ADC2_CH7/GPIO27)
/IO32: H1.7, U1.8 (32K_XP/GPIO32/ADC1_CH4)
/IO33: H1.8, U1.9 (32K_XN/GPIO33/ADC1_CH5)
GND: C1.1, H1.1, J2.4, PC1.2, SW1.2, SW2.2, U1.1 (GND), U1.15 (GND), U1.38 (GND), U1.39 (GND_THERMAL)
unnamed: C1.2, R1.2, SW1.1, U1.3 (EN/CHIP_PU)

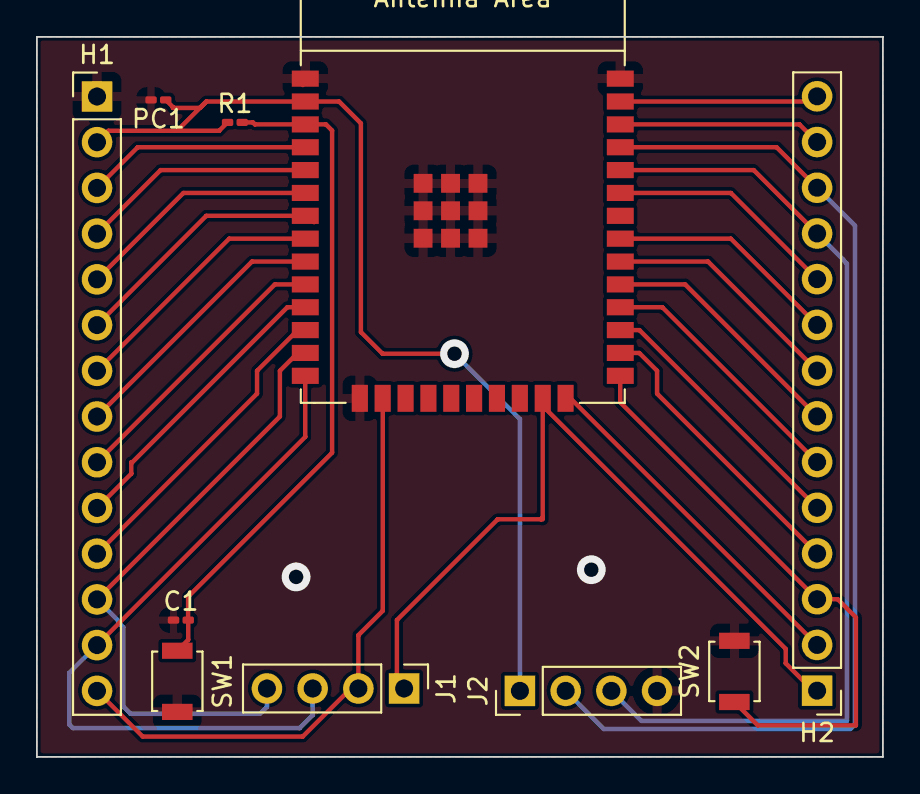
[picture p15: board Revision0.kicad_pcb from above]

Board: 2 copper layers, 47.0 x 40.0 mm, 10 parts (0 on the bottom side), 29 nets.

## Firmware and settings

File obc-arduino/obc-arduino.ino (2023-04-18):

#include <Wire.h>
#include <SPI.h>
#include <SD.h>
#include <Adafruit_Sensor.h>
#include <Adafruit_BMP280.h>
#include <MPU9250_asukiaaa.h>

// Define pins for SD card module
#define SD_CS 5
#define MPU_CS 37
#define BMP_CS 36
#define SI_CS 7
#define SDA_PIN 4
#define SCL_PIN 21


#define LAUNCH_ARM_SECONDS 0

// Initialize SD card object
File dataFile;
File logfile;

// Initialize BMP280 sensor object
Adafruit_BMP280 bmp;

// Initialize MPU9250 sensor object
MPU9250_asukiaaa imu;

// MPU readings
float ax;
float ay;
float az;
float gx;
float gy;
float gz;
float mx;
float my;
float mz;

// SD file index
uint16_t fileIndex = 0;

void setup() {
  Serial.begin(115200);

  // Initialize SD card
  pinMode(SD_CS, OUTPUT);
  if (!SD.begin(SD_CS)) {
    Serial.println("SD card initialization failed!");
    return;
  }
  Serial.println("SD card initialization success.");

  // Log SD card initialization
  logfile = SD.open("/log.txt", FILE_APPEND);
  if (logfile) {
    String logmsg = String(millis()) + " SD card initialization success.";
    logfile.println(logmsg);
    logfile.close();
  } else {
    Serial.println("SD card inoperable!");
    while (1);
  }

  // Generate datafile
  String filename = "/data" + String(fileIndex) +".txt";
  dataFile = SD.open(filename, FILE_WRITE);

  // Init i2c
  Wire.begin(SDA_PIN, SCL_PIN);
  imu.setWire(&Wire);


  // Initialize BMP280 sensor
  if (!bmp.begin(0x76)) {
    log("BMP280 unresponsive!");
  } else {
    log("BMP280 sensor initialised.");
  }

  // Safety window for rocket setup.
  log("Entering launch safety window.");
  int count = LAUNCH_ARM_SECONDS / 10;
  while (count > 0) {
    String ttl = String(count*10) + " seconds remaining till system is armed";
    logMutable(ttl);
    count--;
    delay(10000);
  }

  // Initialize MPU9250 sensor
  imu.beginAccel();
  imu.beginGyro();
  imu.beginMag();

  // Log MPU9250 sensor initialization
  log("MPU9250 sensor initialization success.");

  // Wait for rocket launch
  log("Waiting for rocket launch...");
  float prev_az = 0.0;
  float curr_az = 0.0;
  while (true) {

    if (imu.accelUpdate() == 0);
      curr_az = imu.accelZ();
    // Serial.println(curr_az);
    if (curr_az > prev_az + 1.0) {
      break;
    }
    prev_az = curr_az;
    delay(250);
  }
  Serial.println("Rocket launch detected!");

  // Log rocket launch detection
  logfile = SD.open("/log.txt", FILE_APPEND);
  if (logfile) {
    String logmsg = String(millis()) + " Rocket launch detected!";
    logfile.println(logmsg);
    logfile.close();
  }

}

void loop() {
  // Read data from BMP280 sensor
  float temperature = bmp.readTemperature();
  float pressure = bmp.readPressure();

  // Read data from MPU9250 sensor
  if (imu.accelUpdate() == 0 && imu.gyroUpdate() == 0 && imu.magUpdate() == 0) {
    ax = imu.accelX();
    ay = imu.accelY();
    az = imu.accelZ();
    gx = imu.gyroX();
    gy = imu.gyroY();
    gz = imu.gyroZ();
    mx = imu.magX();
    my = imu.magY();
    mz = imu.magZ();
  }


  // Open a new file every 512 bytes
  if (dataFile.size() >= 500) {
    if (dataFile) {
      dataFile.close();
    }
    String filename = String("/data") + String(fileIndex) + String(".txt");
    fileIndex++;
    dataFile = SD.open(filename, FILE_WRITE);
    if (!dataFile) {
      String err = "Error opening file for writing - file "+ filename; 
      logMutable(err);
      return;
    } else {
      String msg = "File #" + String(fileIndex -1) + " finished. Starting " + filename;
      logMutable(msg);
    }
  }

  // Write data to file
  dataFile.print(temperature);
  dataFile.print(",");
  dataFile.print(pressure);
  dataFile.print(",");
  dataFile.print(millis());
  dataFile.print(": ");
  dataFile.print(ax);
  dataFile.print(",");
  dataFile.print(ay);
  dataFile.print(",");
  dataFile.print(az);
  dataFile.print(",");
  dataFile.print(gx);
  dataFile.print(",");
  dataFile.print(gy);
  dataFile.print(",");
  dataFile.print(gz);
  dataFile.print(",");
  dataFile.print(mx);
  dataFile.print(",");
  dataFile.print(my);
  dataFile.print(",");
  dataFile.println(mz);

  // Flush data to SD card
  dataFile.flush();
}


void log(const char* msg) {
  logfile = SD.open("/log.txt", FILE_APPEND);
  if (logfile) {
    String logmsg = String(millis()) +": " + msg;
    logfile.println(logmsg);
    logfile.close();
    Serial.println(logmsg);
  }
}

// Log a message to the SD card and serial, but for mutable C++ strings
void logMutable(String s) {
  logfile = SD.open("/log.txt", FILE_APPEND);
  if (logfile) {
    String logmsg = String(millis()) +": " + s;
    logfile.println(logmsg);
    logfile.close();
    Serial.println(logmsg);
  }
}

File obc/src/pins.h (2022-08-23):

// Pin outs for ESP32
// Matt Rossouw (omeh-a)
// 08/22
#pragma once

#define THERMISTOR_PIN_1 A0
#define THERMISTOR_PIN_2 A1
#define THERMISTOR_PIN_3 A2
#define THERMISTOR_PIN_4 A3
#define BAROMETER_PIN A4
#define ACCELOROMETER_SPI_CS_PIN 0000
#define ACCELOROMETER_SPI_MOSI_PIN 0000
#define ACCELOROMETER_SPI_MISO_PIN 0000

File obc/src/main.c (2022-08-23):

// Bluesat22 primary microcontroller Rocketry collab 10,000ft test flight
// Matt Rossouw (omeh-a) Priyanta Islam ()
// 08/22

#include "main.h"

// Buffers stored as byte fields to avoid heap operations. This may or may not work.
static char sd_buffer[BUFFER_SIZE * sizeof(buffer_entry_t)];
static char flash_buffer[BUFFER_SIZE * sizeof(buffer_entry_t)];

unsigned int buffer_index = 0;
unsigned int failure_buffer_index = 0;

int main(char *argv[], int argc) {
    
    // Initialise buffers - set each entry to 0
    for (int i = 0; i < BUFFER_SIZE * sizeof(buffer_entry_t); i++) {
        sd_buffer[i] = 0;
    }
    for (int i = 0; i < BUFFER_SIZE * sizeof(compact_buffer_entry_t); i++) {
        flash_buffer[i] = 0;
    }

    // Perform device initialisation
    deviceInit();

    // Initialise onboard flash
    flashwrite_init();

    // Initialise SD card
    sdcard_init();
    
    // Wait until accelerometer registers launch
    launchWait();

    // Start data collection
    mainLoop();

    return 0;
}

/*  @brief main loop of sensing, communicating and data logging
 *  @return 
*/
void mainLoop(void) {
    while (1) {
        buffer_entry_t *entry = (buffer_entry_t*)&sd_buffer[buffer_index * sizeof(buffer_entry_t)];        

        // Read RTC
        //TODO
        
        // Read accelerometer
        accelRead(entry);

        // Read IMU

        // Read analog inputs
        //TODO


        // write to SD card
        int err = writeSD();
        if (err) goto sd_fatal;
    }

    return;

sd_fatal:
    // If the SD card is misbehaving, immediately terminate communication to
    // protect stored data. Poll sensors at a much slower rate and utilise backup
    // storage onboard ESP
    
    // Don't touch the previously bufferred data.
    while (1) {
        // TODO: wait for 1 second using ESP32 RTOS

        // Get pointer to buffer entry
        compact_buffer_entry_t *entry = (compact_buffer_entry_t*)&flash_buffer[failure_buffer_index * sizeof(compact_buffer_entry_t)];

        // Read RTC
        //TODO

        // Read accelerometer
        compact_accelRead(entry);

        // Read IMU
        //TODO

        // Commit to flash
        flashwrite(entry);
        
    }
    

    return;
}

void deviceInit() {

}

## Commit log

2022-08-10 Upload of cubesat structure and battery
    [1U CubeSat.0001.iam, 1U CubeSat.iam, 1U_Satellite.0007.iam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]
2022-08-10 Updated Assembly
    [BatteryPack.0003.iam, BatteryPack.0004.iam, BatteryPack.iam]
2022-08-10 Added a battery pack slide in design
    [BatteryHolderEndSeries_v2.ipt, BatteryHolderEnd_v2.ipt, BatteryPack_v2.iam]
2022-08-17 Added Layout for Elec in terms of structure
    [1U_Satellite.0007.iam, 1U_Satellite.0009.iam, 1U_Satellite.iam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]
2022-08-19 STLs made
    [1U_Satellite.0009.iam, 1U_Satellite.0010.iam, 1U_Satellite.iam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]
2022-08-20 Power and ESP breakout
    Power board added.
    ESP board made
    [1U power board.kicad_pcb, 1U power board.kicad_sch, Revision0.kicad_pcb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]
2022-08-21 function for writing to sd card from esp32
2022-08-23 Merged buffering branch, added arduino code for gy91
2022-11-19 Overdue electronics changes
    [1U power board.kicad_pcb, 1U power board.kicad_sch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]
2022-12-09 Setup
    Adding finished and WIP boards, creating a libraries folder that can be synced across all users
    [1U power board.kicad_pcb, 1U power board.kicad_sch, Battery Board.kicad_pcb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]
2022-12-09 Battery Protection Circuit
    [Battery Board.kicad_pcb, Battery Board.kicad_sch]
2022-12-09 Battery protection circuit added
    [Battery Board.kicad_pcb]
2022-12-11 Batter Board almost finished
    TODO
    - Change mosfets&shunt resistor to new choice
    - Adjust inductor for higher voltage
    [Battery Board-B_Cu.gbr, Battery Board-B_Mask.gbr, Battery Board-B_Paste.gbr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]
2022-12-15 Finalised PCB, working schematic
    Sending to Fab tomorrow, schematic could do with a little cleanup.
    [Battery Board-B_Cu.gbr, Battery Board-B_Mask.gbr, Battery Board-B_Paste.gbr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]
2023-03-21 Long overdue commit
    [Sensor Board.kicad_pcb, Sensor Board.kicad_sch, Sensors.kicad_pcb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]
2023-04-17 Replaced arduino sketch
